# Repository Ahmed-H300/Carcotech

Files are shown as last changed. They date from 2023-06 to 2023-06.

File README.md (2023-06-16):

# Table of content
  * [preface](#preface)
  * [car design](#car-design)
  * [components, prices and links](#components-prices-and-links)
  * [schematics](#schematics)
  * [demo videos](#demo-videos)
  * [android app](#android-app)
  * [Important Notes](#Important-Notes)

# preface

<details>
<summary> click to view...</summary>

our problem statment was to create a car that follows a line without drifting out of the line and traverse a maze to find a specific path from end to end, the car have a small user interface via buttons, can play song and produce various patterns on strip of neopixel leds while traversing the maze or running on the line tracker, all without affecting the main functionality of the car, this wouldn't have been possible without the help of freeRTOS and espressif-idf.

### An autonomous car that can follow a line, solve maze and find it's path out. 
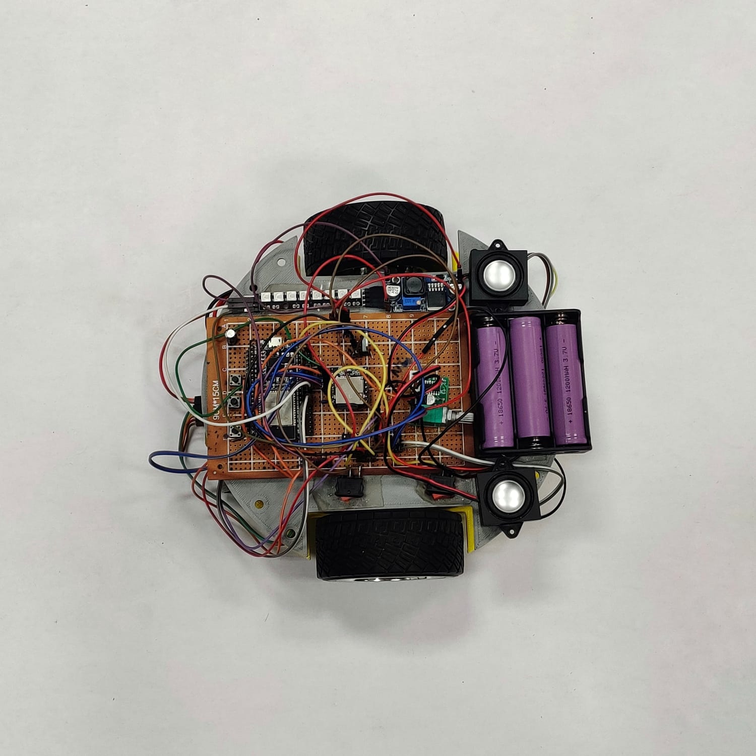
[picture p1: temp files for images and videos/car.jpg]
our lovely car


### shape of line tracker that was given to us to train on 
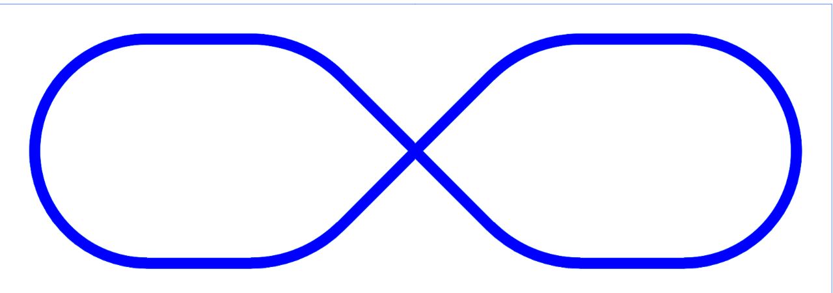
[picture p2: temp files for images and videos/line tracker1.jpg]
line tracker1


### shape of line tracker that was given on compitition day 
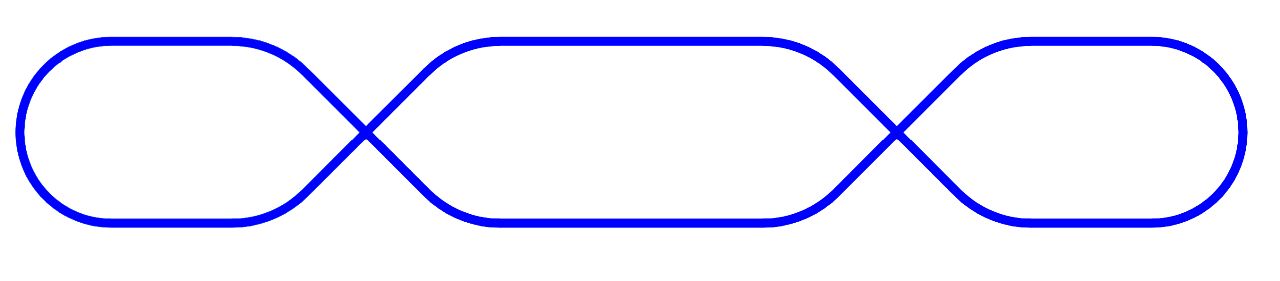
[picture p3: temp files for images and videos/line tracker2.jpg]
line tracker2


### shape of maze that was given to us and used on competition day
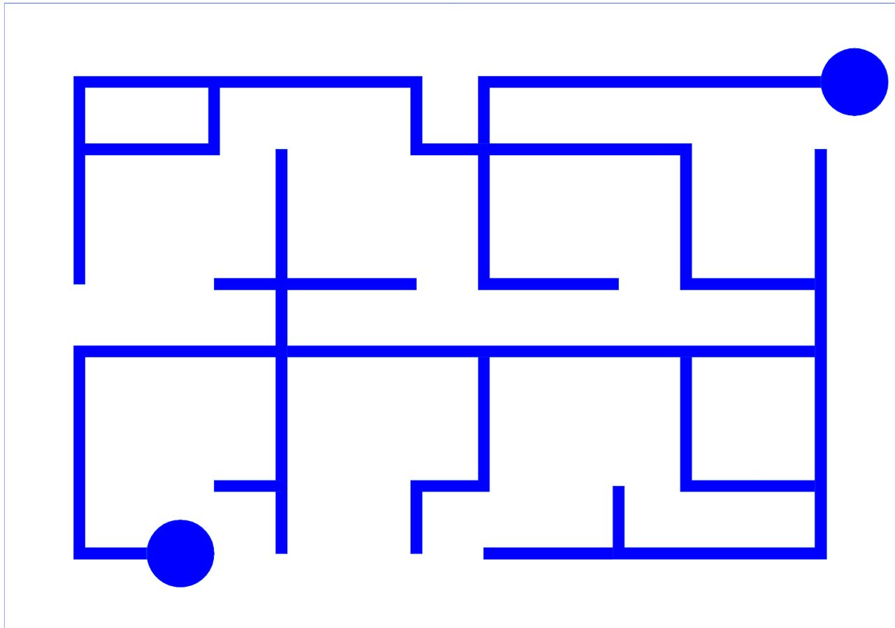
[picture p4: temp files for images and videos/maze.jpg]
maze


</details>

# car design

<details>
<summary> click to view...</summary>

- we used [freeCAD](https://www.freecad.org/) to design our car body, the design files can be found in [3D car design files/freeCAD-project files](./3D%20car%20design%20files/freeCAD-project%20files/) and you can open it using freeCAD, at first we designed the car to be of 3 floors and designed a holder for the sensor but after printing a prototype of the design, it was found that files called `third floor.FCStd` and `first_floor.FCStd` are only the useful file and all of the rest of design files were not used for the sake of this project.

- to print the 3d design, you need to generate STL files from your design (was done by freeCAD also), so the generated stl files are found in [3D car design files/stl files for 3 printing](./3D%20car%20design%20files/stl%20files%20for%203%20printing/) where `1st - floor.stl` and `3rd - floor.stl` are only files that we printed where each files is printed alone and you shall send the `.stl` files to the 3D printing service company not the `.FCStd` files.

- we made a custom design not a readily printed one as we needed a custmized shape, surface area and customized space for PCB and 2 motors, we choosed a circular shape as it seems to be a nice modern shape and it was inspired by [Pololu car](https://www.youtube.com/watch?v=mJV-KDqHgDQ)

## image of the final designed
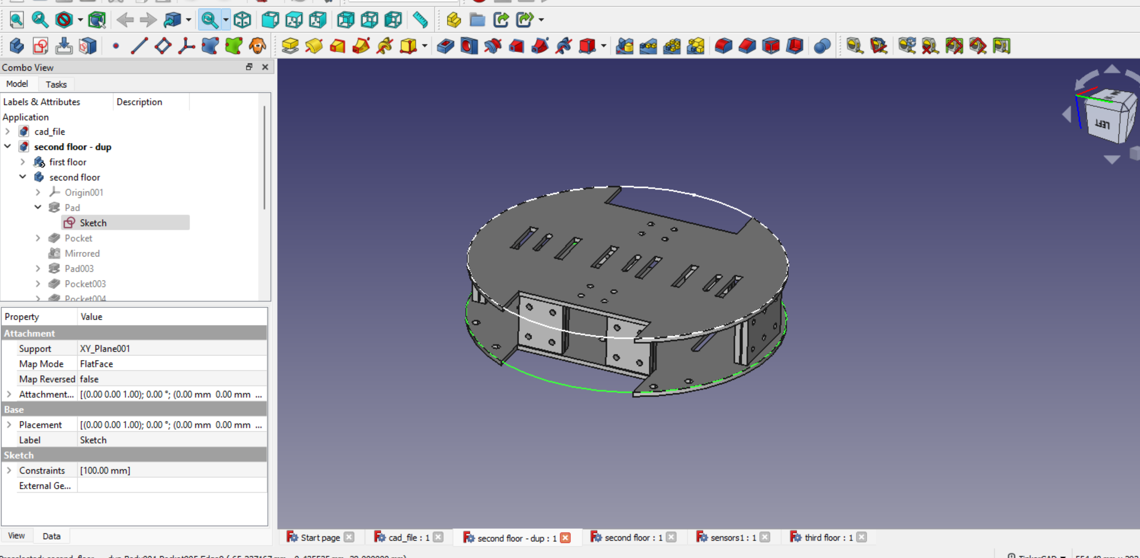
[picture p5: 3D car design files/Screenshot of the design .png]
final car body


</details>

# components, prices and links

<details>
<summary> click to view...</summary>

you can find the list of components with prices in the directory called [prices & components used](./prices%20%26%20components%20used/) in the `prices and components list.pdf` or `prices and components list.xlsx` but it's not mentioned where we purchased these components and the prices doesn't include custom costs nor the shipping prices.

**if you have time, we recommend you to purchase all of the components from ali express as it's cheaper in prices** 

| component | no.of items | unit price | link | extra details|
| :--- | :----: |  :----: | :--- | :--- |
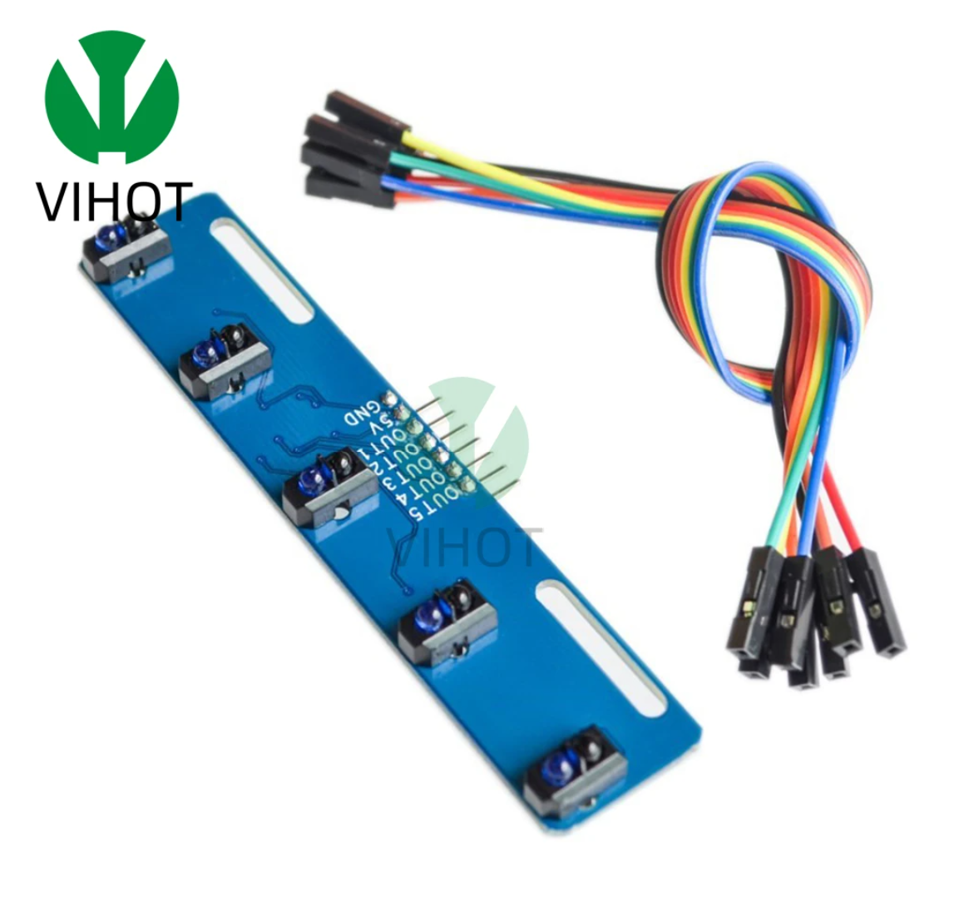
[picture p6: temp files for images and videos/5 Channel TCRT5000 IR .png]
5 Channel TCRT5000 IR
| 5 Channel TCRT5000 IR  | 2 | 50 EGP | https://www.aliexpress.com/item/1005004984933041.html?spm=a2g0o.order_list.order_list_main.25.21ef1802DzQBHj | used to detect line, intersections, path, etc...| 5 Channel TCRT5000 IR |
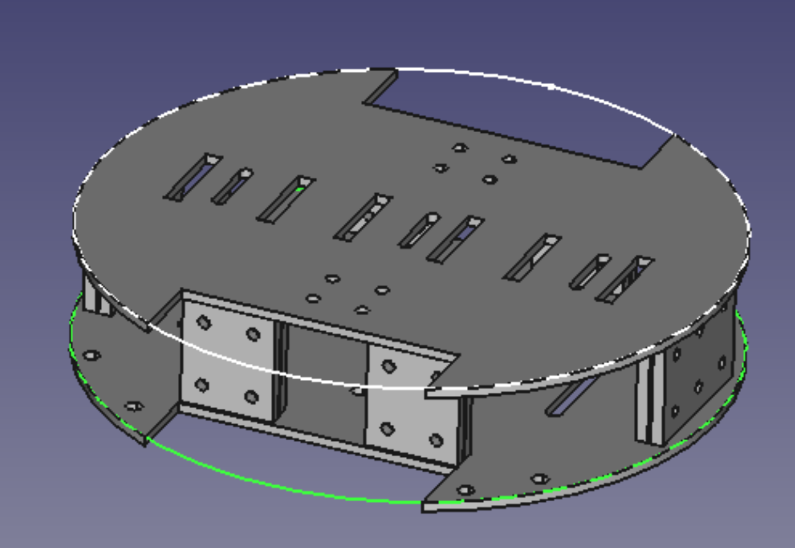
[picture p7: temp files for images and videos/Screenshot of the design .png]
3D printing (Car Chassis)
| 3D printing (Car Chassis)  | 1 | 460 EGP | https://wa.me/+201228206436 and https://wa.me/+201203414479 | this is the car body, there are plenty of companies, individuals whom provide 3d printing services, but these 2 numbers are for students who provide 3d printing services for a good quality with cheap prices | 3D printing (Car Chassis)
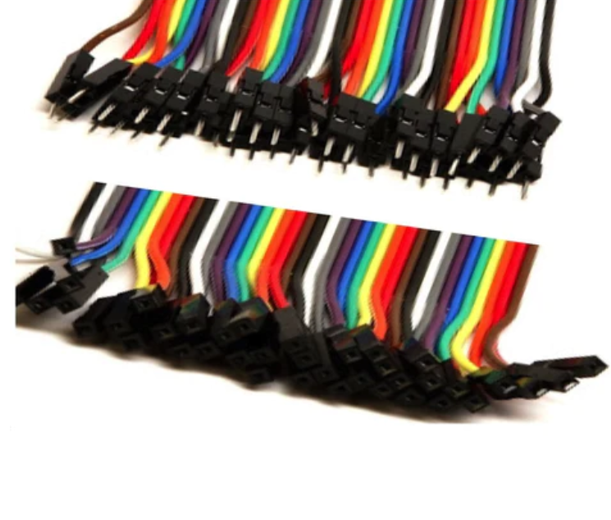
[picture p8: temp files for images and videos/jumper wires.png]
wires
| wires  | 40 | 1 EGP | https://store.fut-electronics.com/search?type=product&q=jumper+wire | was used to connect compoents with each other, future electronics provides jumper wires with many different lengths ( we used 30 cm and 20 cm wire) | wires
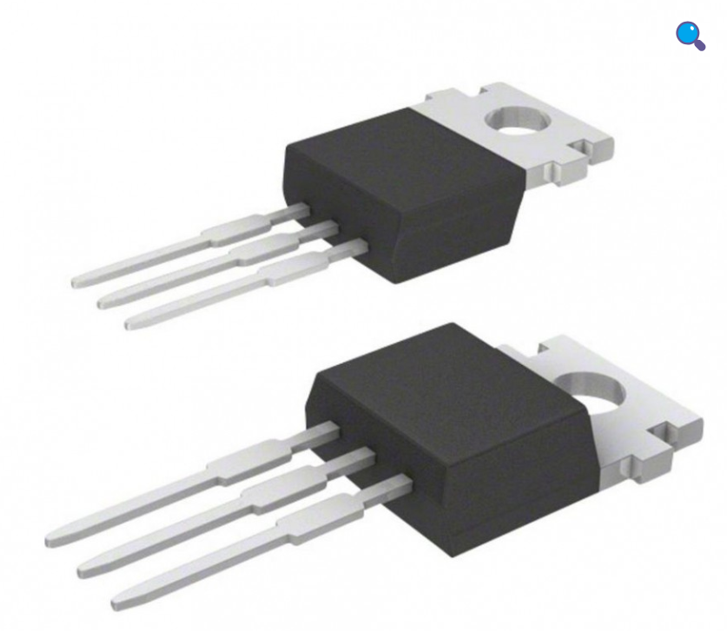
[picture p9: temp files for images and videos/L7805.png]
voltage regulator (L7805)
| voltage regulator (L7805)  | 1 | 4.5 EGP | https://free-electronic.com/product/l7805cv/ | supplied esp32 with the power supply of 5V, we had to insulate the power source of esp32 from other components as speakers made small fluctuations in the power source which made esp32 to reset several times | voltage regulator (L7805)|
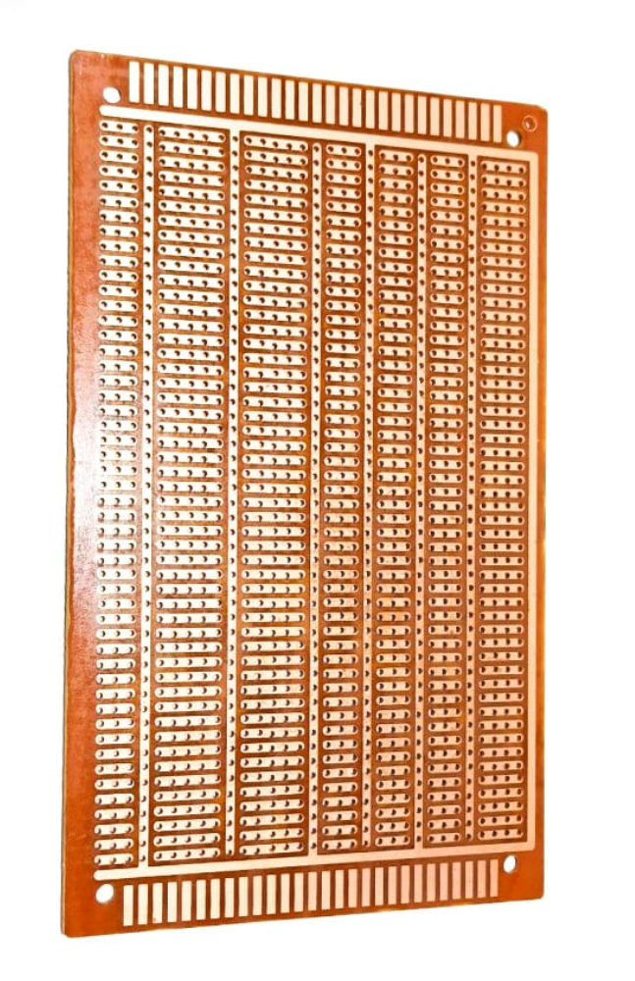
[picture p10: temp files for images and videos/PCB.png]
PCB Bread Board Shape FR2 (9X15 cm2)
| PCB Bread Board Shape FR2 (9X15 cm2)  | 2 | 15 EGP | https://free-electronic.com/product/pcb-bread-board-shape-fr2-9x15-cm2-horizontal/ | we used a prototype pcb which is more reliable than solderless board | PCB Bread Board Shape FR2 (9X15 cm2) |
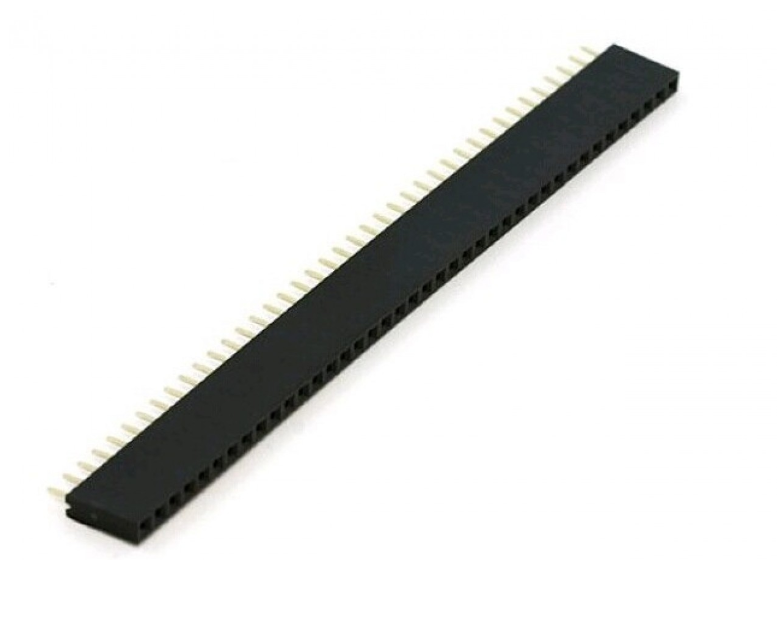
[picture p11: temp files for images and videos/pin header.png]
pin header
| pin header  | 8 | 4 EGP | https://free-electronic.com/?s=pin+header&product_cat=0&post_type=product | needed pin headers to be soldered onto prototype pcb (we mainly used female pin header and rarely male pin headers) | pin header |
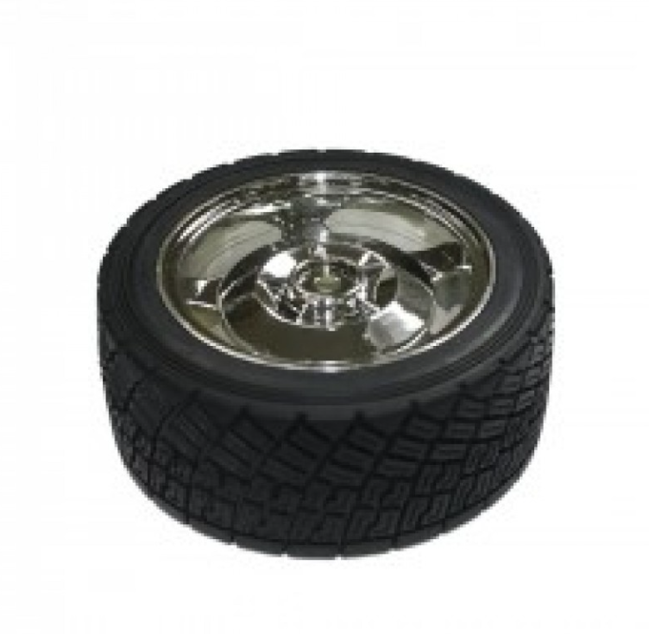
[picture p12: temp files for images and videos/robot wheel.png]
Robot Car Wheel 85mm
| Robot Car Wheel 85mm  | 2 | 85 EGP |  https://free-electronic.com/product/robot-car-wheel-85mm/ | this was the perfect wheel for our car body the provided needed height from the ground | Robot Car Wheel 85mm | 
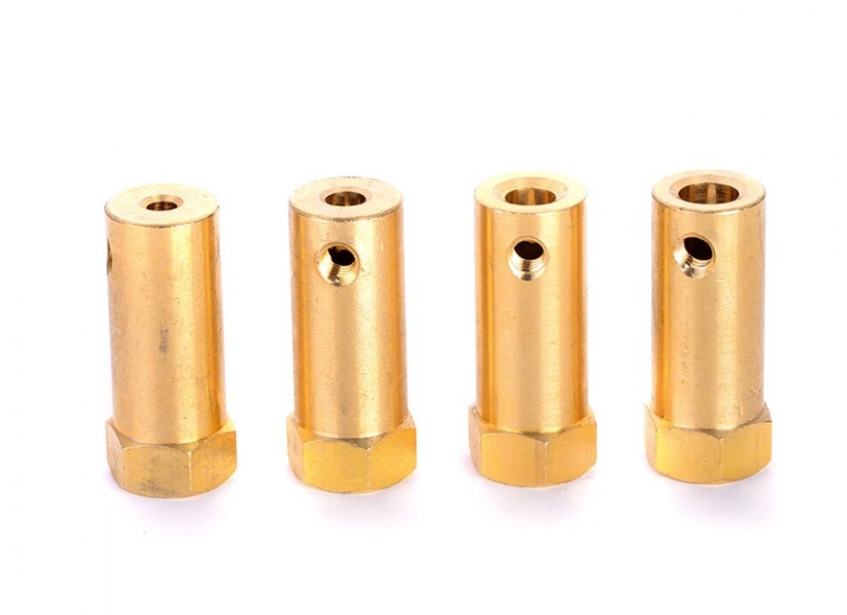
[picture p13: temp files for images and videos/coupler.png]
Metal Coupler 4mm
| Metal Coupler 4mm  | 2 | 35 EGP | https://free-electronic.com/product/metal-coupler-4mm-short-coupling-for-robot-smart-car-wheel/ |  was used to connect the motors to the wheels | Metal Coupler 4mm |
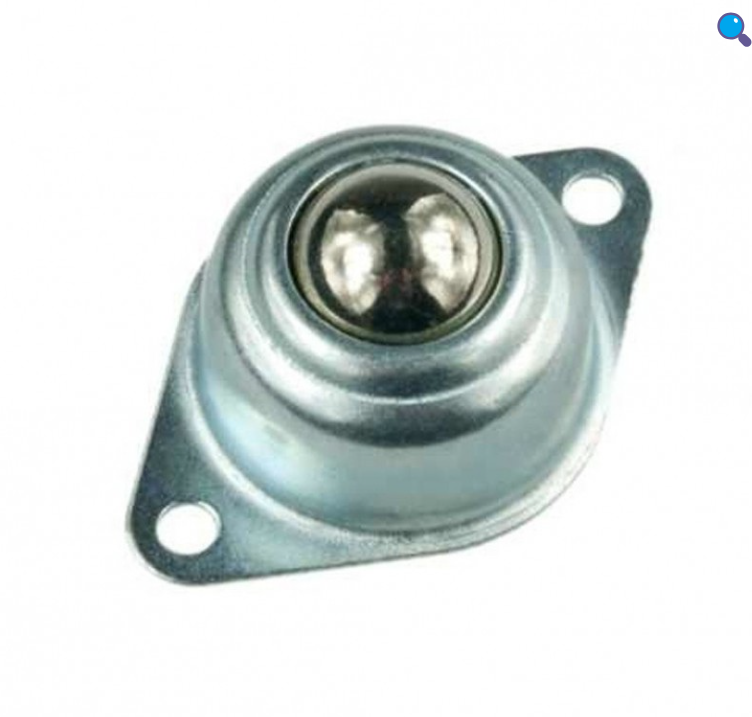
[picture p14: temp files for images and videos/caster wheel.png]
Metal Caster Wheel for Robot (20mm)
| Metal Caster Wheel for Robot (20mm)  | 2 | 35 EGP | https://free-electronic.com/product/metal-caster-wheel-for-robot-20mm/ | since car has only 2 motors so we needed 2 caster wheel to support car body from beneath to prevent it from swinging | Metal Caster Wheel for Robot (20mm) |
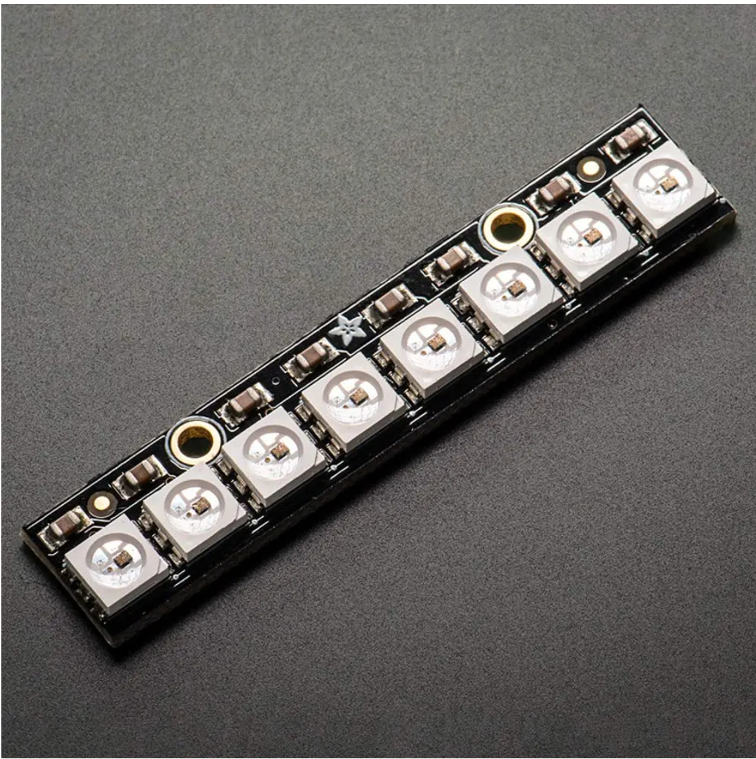
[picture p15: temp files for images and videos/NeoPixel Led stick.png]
NeoPixel Led stick
| NeoPixel Led stick  | 1 | 200 EGP | https://www.aliexpress.com/i/4000203985307.html | I bought this component before a year from ram-electronics but it seems now it's not available on ram any more but it's available on ali express | NeoPixel Led stick
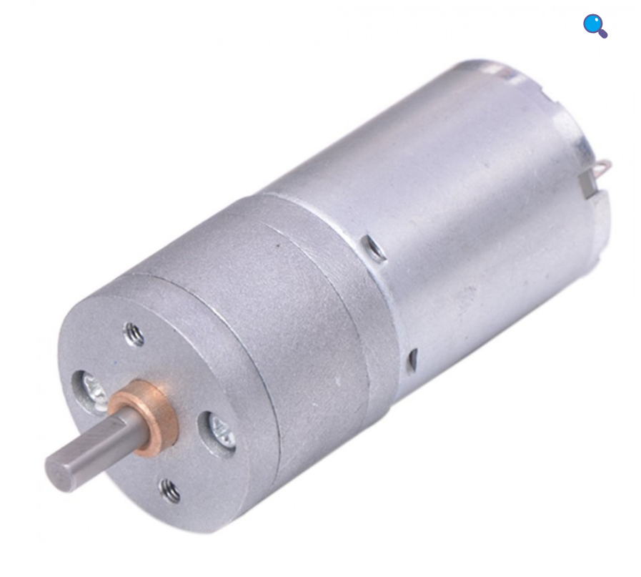
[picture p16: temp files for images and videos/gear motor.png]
DC Gear Motor (8.8KG ) 250RPM
| DC Gear Motor (8.8KG ) 250RPM   | 2 | 325 EGP | https://free-electronic.com/product/dc-gear-motor-8-8kg/ | criteria of selection of our gear motor is that it has high reduction ration with high torque and high rpm but note that rpm is inversely proportional to reduction ratio so our motor had torque of 8.8 KG with rpm = 250 RPM and reduction ration 25:1 but it worked perfectly | DC Gear Motor (8.8KG ) 250RPM
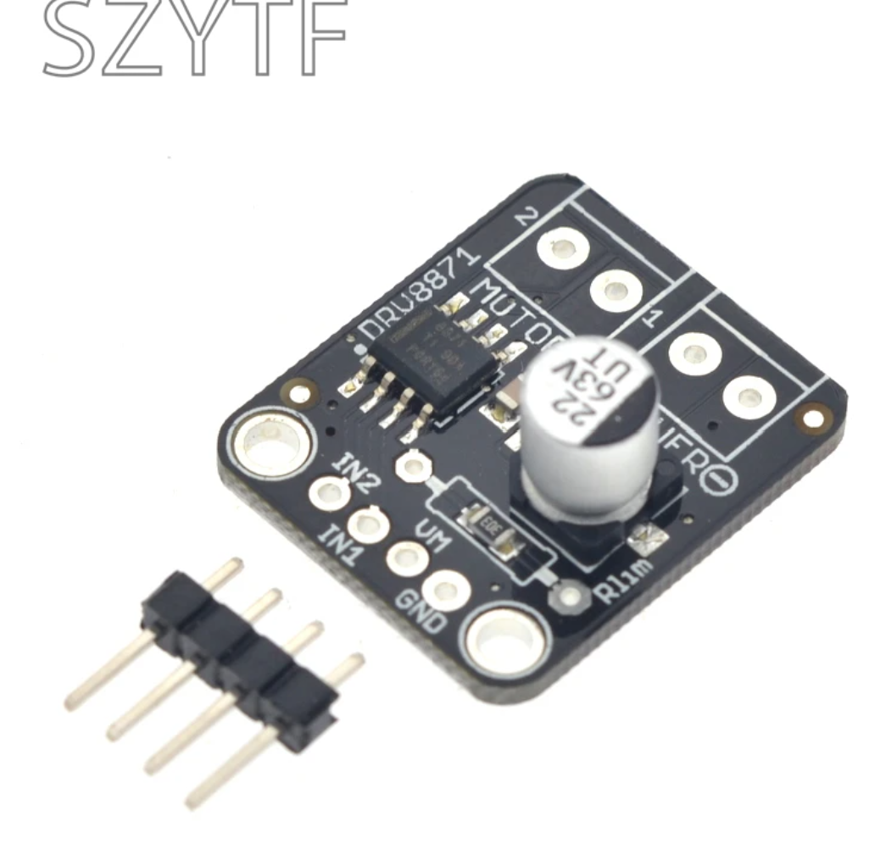
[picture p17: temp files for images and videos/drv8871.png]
Motor driver DRV8871
| Motor driver DRV8871  | 2 | 130 EGP | https://www.aliexpress.com/item/1005001590487986.html?spm=a2g0o.order_list.order_list_main.40.21ef1802DzQBHj | motor driver small chip where one chip controls one motor so we needed 2, this is better than L298 as it's smaller, can pass higher current | Motor driver DRV8871 |
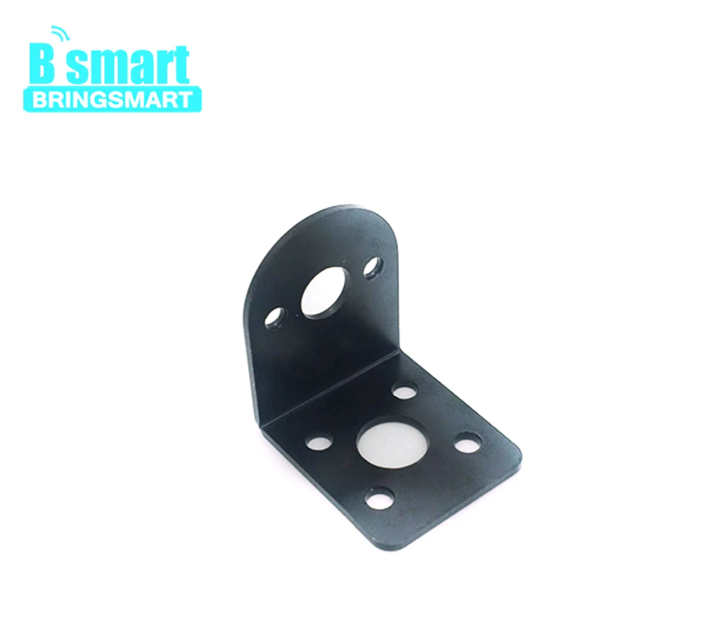
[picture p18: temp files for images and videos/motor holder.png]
Screw Mounting Bracket
|  Screw Mounting Bracket  | 2 | 50 EGP | https://www.aliexpress.com/item/32856826638.html?spm=a2g0o.order_list.order_list_main.89.21ef1802DzQBHj | used to hold the motor onto the car body | Screw Mounting Bracket |
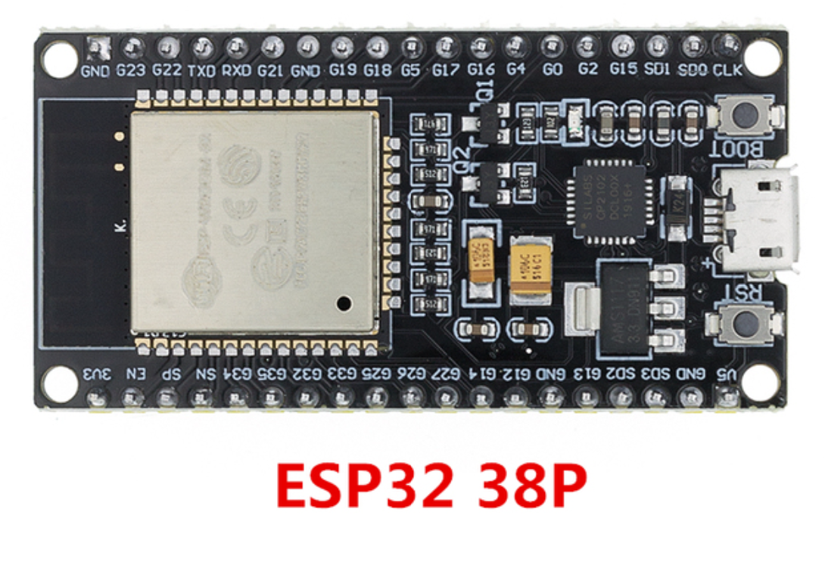
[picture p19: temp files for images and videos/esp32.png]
ESP32 Development Board
| ESP32 Development Board  | 1 | 150 EGP | https://www.aliexpress.com/item/1005001621773806.html?spm=a2g0o.order_list.order_list_main.95.21ef1802DzQBHj | this was our main MCU and we recommend using it over arduino as it has many useful features like its espressif-idf that comes with freeRTOS, dual core, high speed MCU (240 MHZ), integrated wifi and integrated bluetooth on chip| ESP32 Development Board |
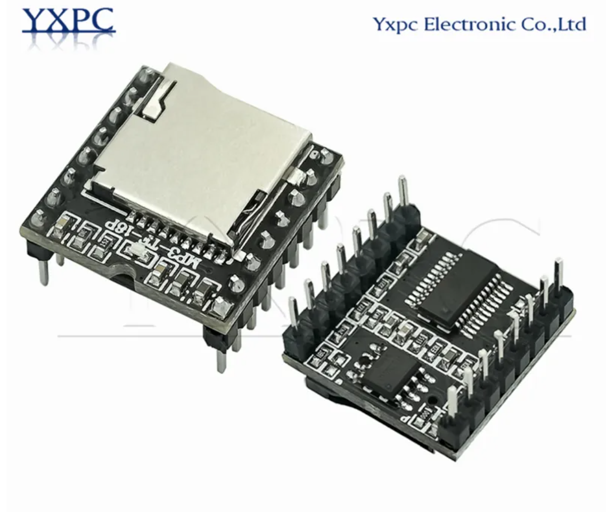
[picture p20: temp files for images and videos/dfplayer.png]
DFPlayer Mini MP3
| DFPlayer Mini MP3  | 1 | 50 EGP | https://www.aliexpress.com/item/1005004994130177.html?spm=a2g0o.order_list.order_list_main.70.21ef1802DzQBHj | a chip that plays mp3 audios without need of continous interaction with MCU, you just give it mp3 file number using MCU and it will play it for you | DFPlayer Mini MP3 |
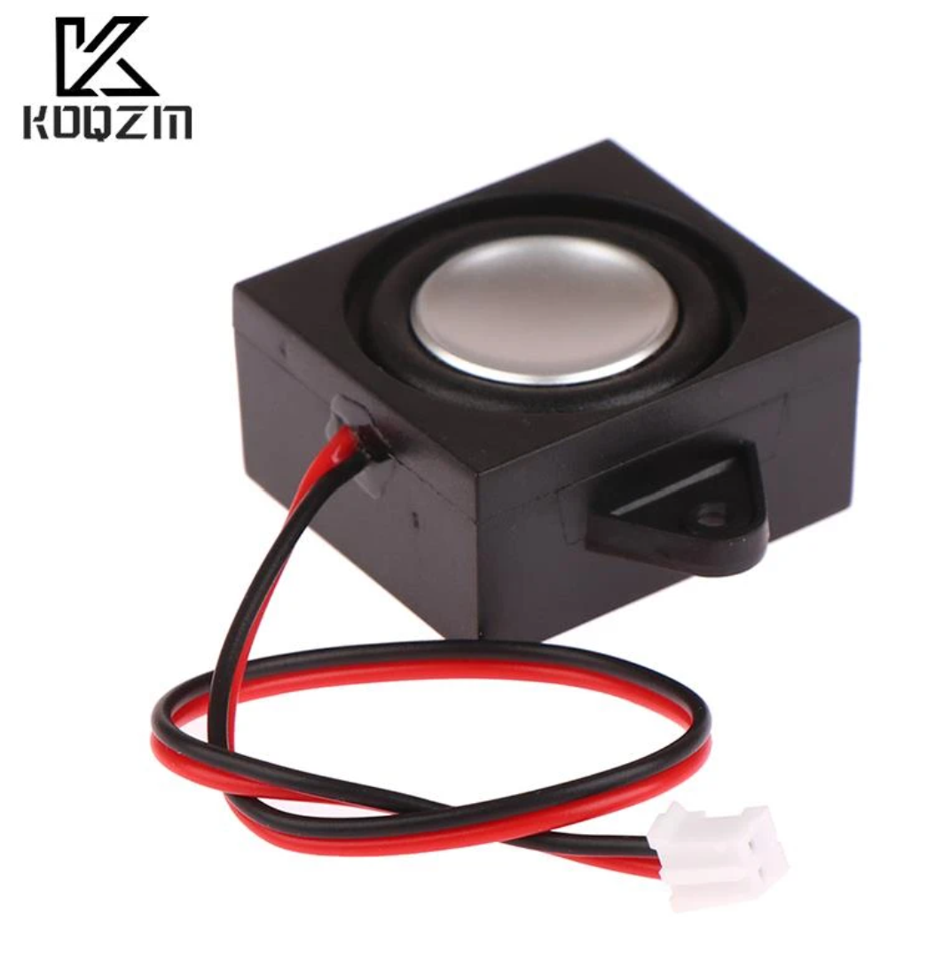
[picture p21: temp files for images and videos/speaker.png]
Speaker 4 Ohm 3 Watt
| Speaker 4 Ohm 3 Watt  | 2 | 55 EGP | https://www.aliexpress.com/item/1005005020984275.html?spm=a2g0o.order_list.order_list_main.15.21ef1802DzQBHj | speakers used to output sound and music while traversing | Speaker 4 Ohm 3 Watt |
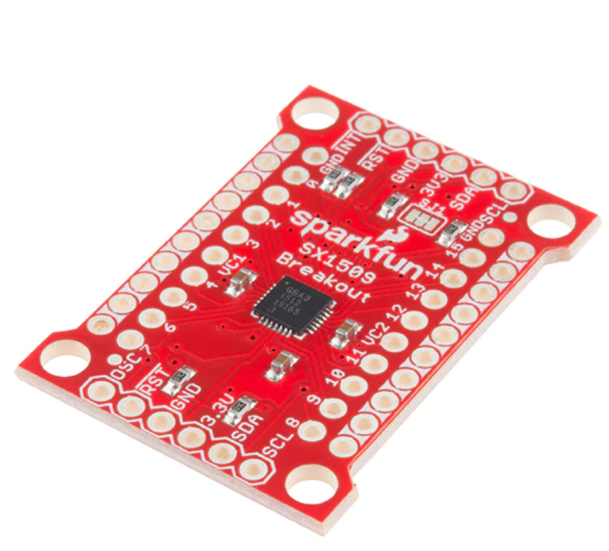
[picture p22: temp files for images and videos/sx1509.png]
I/O Expander Breakout - SX1509
| I/O Expander Breakout - SX1509  | 1 | 85 EGP | https://store.fut-electronics.com/products/copy-of-bi-directional-voltage-level-translator-shifter-txb0104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 | since the amount of pins on esp32 wouldn't be enough for all components, we used a port expander that communicates with esp32 through I2C that will increase the number of pins available | I/O Expander Breakout - SX1509 |
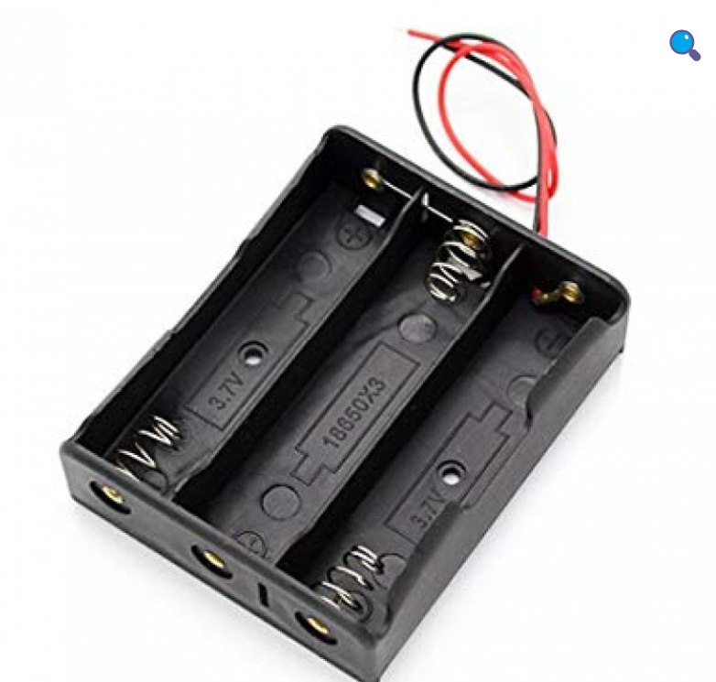
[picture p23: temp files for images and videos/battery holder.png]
battery holder ( 3 x 18650 )
| battery holder ( 3 x 18650 )  | 1 | 15 EGP | https://free-electronic.com/product/battery-holder-3-x-18650/ | holder for lithium batteries as our car runs on 3 lithium batteries | battery holder ( 3 x 18650 ) |
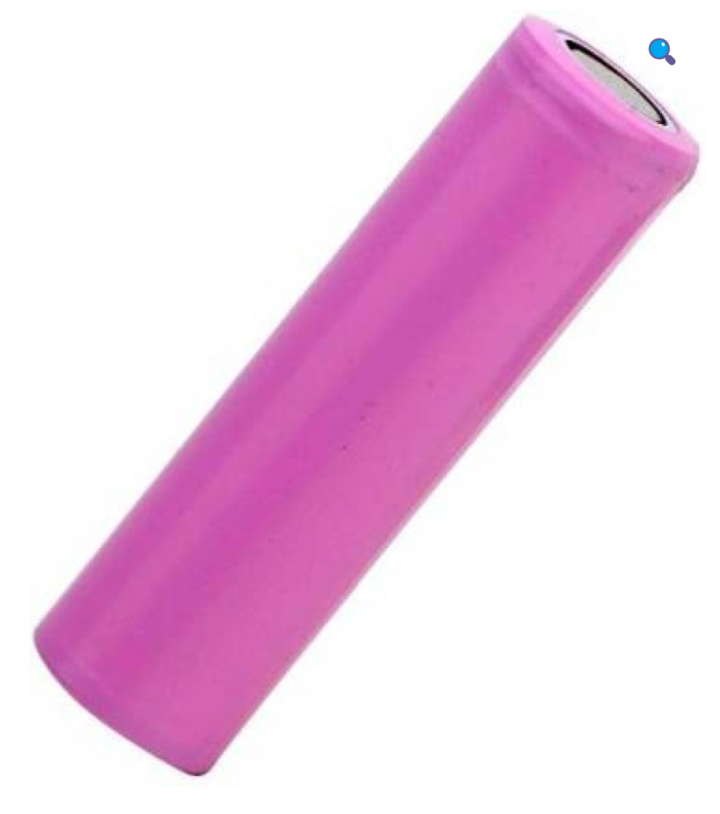
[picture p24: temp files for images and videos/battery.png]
Rechargeable Li-ion Battery18650
| Rechargeable Li-ion Battery18650  | 3 | 50 EGP | https://free-electronic.com/product/rechargeable-li-ion-battery18650-3-7v-1200mah/ | used as power source for the car | Rechargeable Li-ion Battery18650 | 
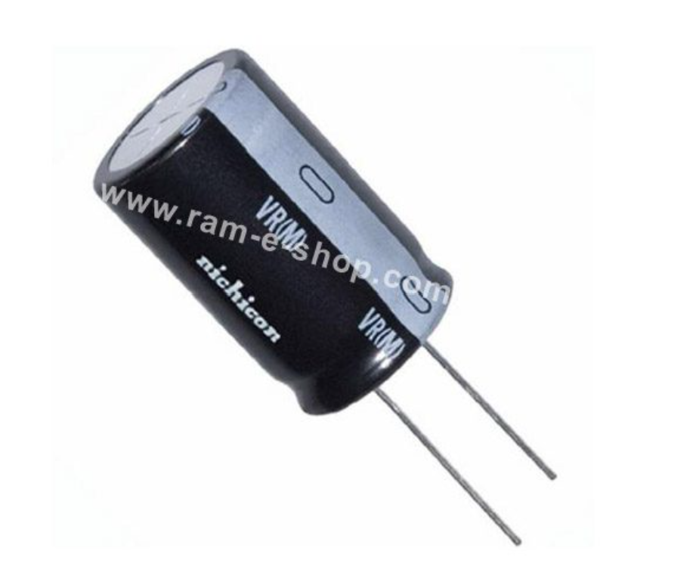
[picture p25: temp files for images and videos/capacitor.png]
electrolytic capacitor
| electrolytic capacitor (25V - 60 micro farad)  | 1 | 3 EGP | https://ram-e-shop.com/product/c-47u250v/ | was used to be connected between 3.3v and GND that helps in power source stability | electrolytic capacitor |
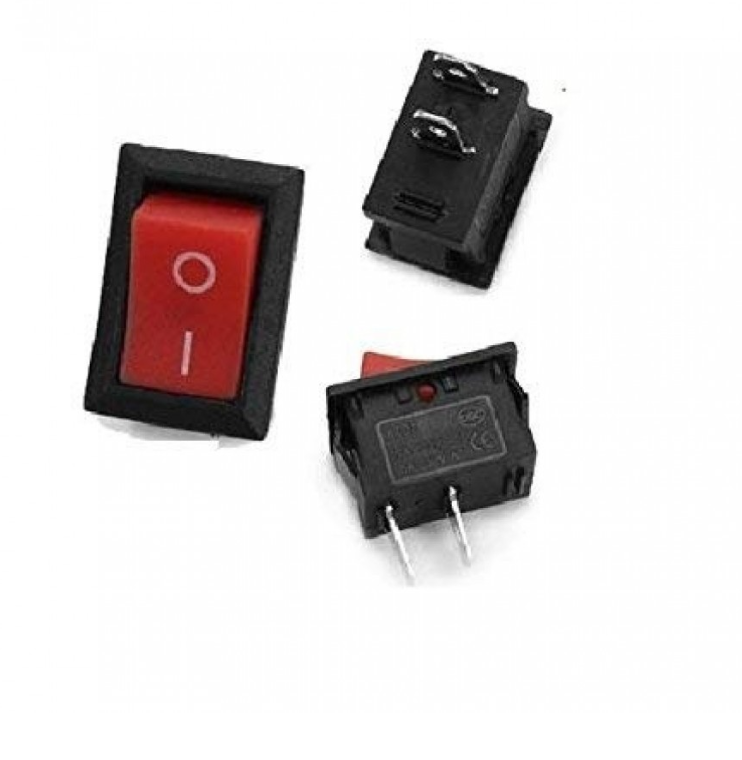
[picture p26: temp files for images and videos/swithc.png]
switch
| switches   | 2 | 1.5 EGP | https://free-electronic.com/product/boat-rocker-switch-on-off-6a250vac-kcd1/ | one used to switch on/off the battery from the system and second one to switch on/off esp32 from the system | switch |
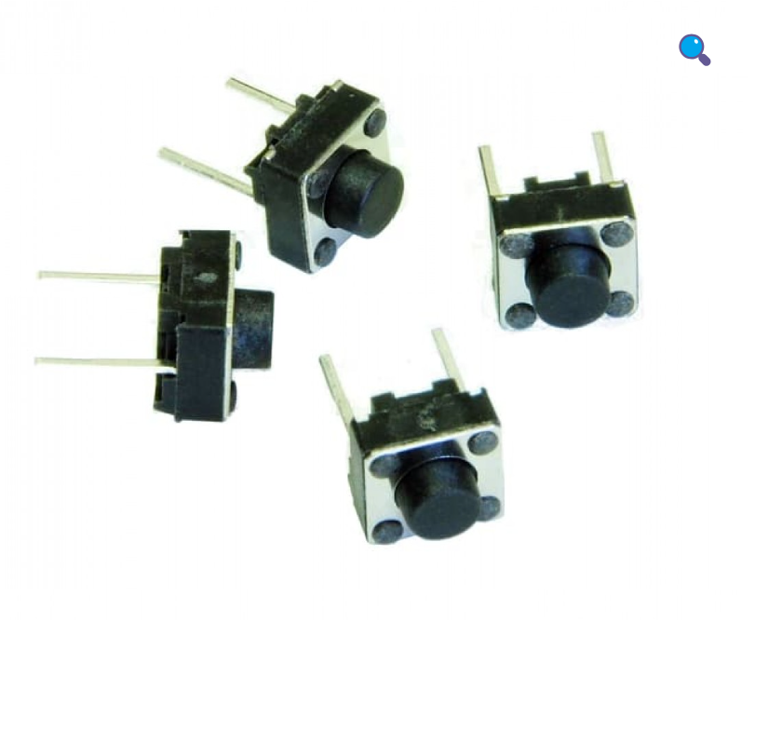
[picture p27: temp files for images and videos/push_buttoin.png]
push button
| push buttons  | 3 | 0.75 EGP | https://free-electronic.com/product/press-2pin-6x6/ | used as user interface , 1 for Line tracker (L) , 1 for maze trainer (M_t) , 1 for maze solver (M_s) | push button |
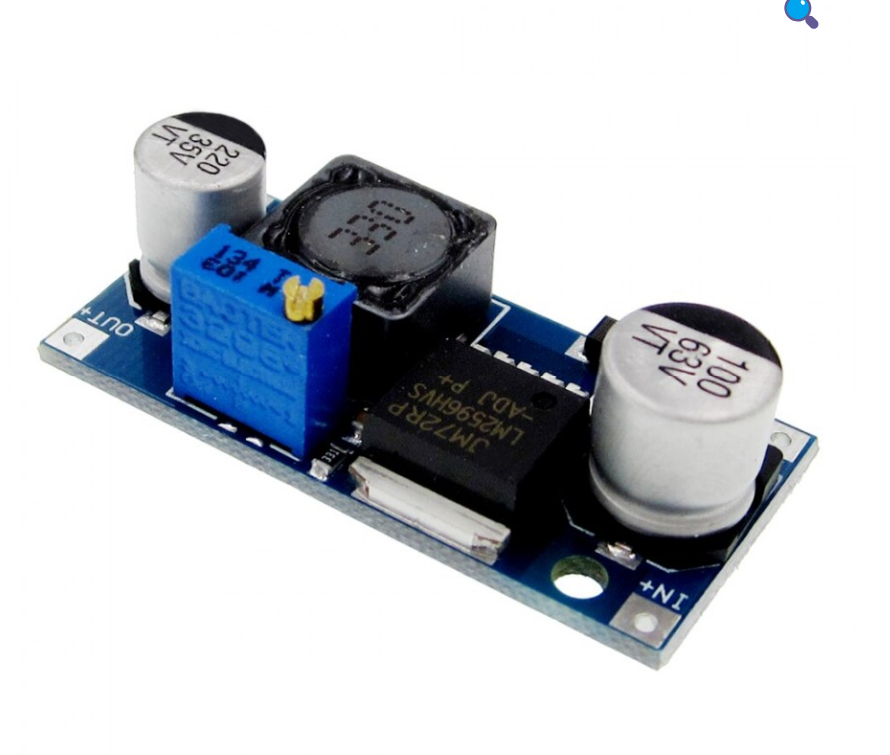
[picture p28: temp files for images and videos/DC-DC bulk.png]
DC-DC Step-Down Module
| LM2596HVS-ADJ DC-DC Step-Down Module (3A)  | 1 | 60 EGP | https://free-electronic.com/product/lm2596hvs-adj-dc-dc-step-down-module-3a/ | used to convert power supply from batteries (around 11 volt) to 3.3V to supply all the system of the car except esp32 that's supplied by voltage regulator and we didn't use voltage regulator to supply the whole system as the whole system withdraw a high amount of current and the maximum that a voltage regulator can supply is about 1 A| DC-DC Step-Down Module|
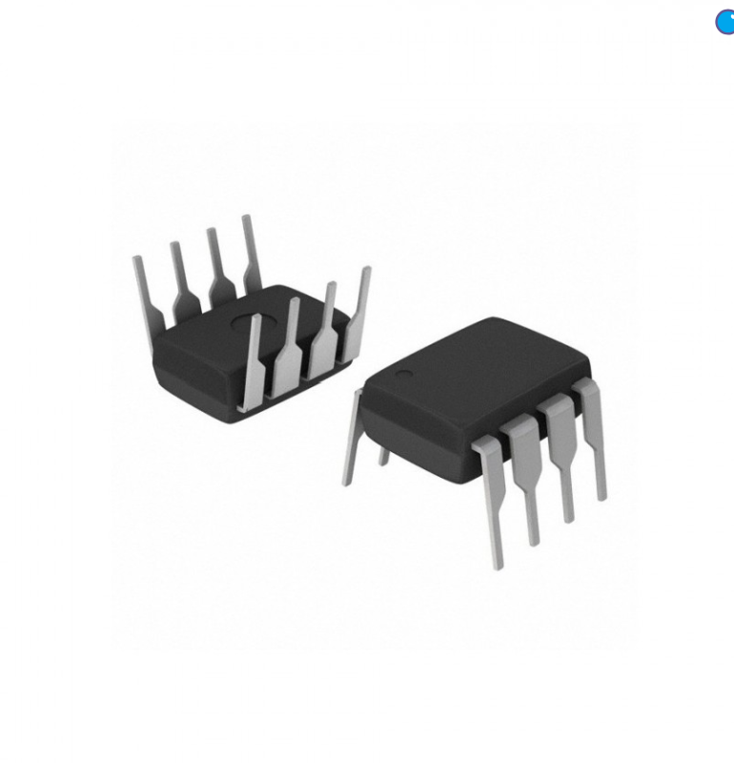
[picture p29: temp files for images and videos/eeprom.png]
EEPROM
| external EEPROM - 32 Kilo-byte (24C256)  | 1 | 25 EGP | https://free-electronic.com/product/24c256/ | was used to store the optimized path after traversing the maze as Esp32 doesn't have interal EEPROM so we bought external one to store the optimized path on it so that if the system shutdown (car was turned off), we don't have to train again as the path is already stored | EEPROM |
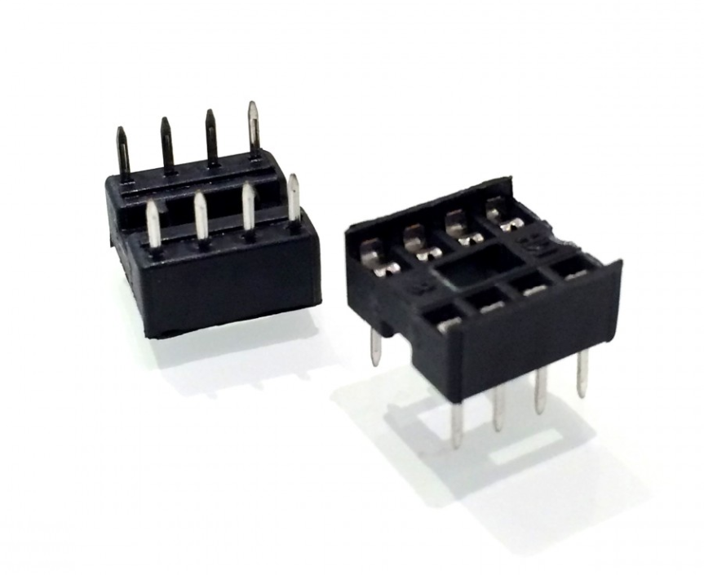
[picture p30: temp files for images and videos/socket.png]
IC socket
| IC SOCKET Base 8 PIN DIP for eeprom  | 1 | 0.5 EGP | https://free-electronic.com/product/ic-socket-base-8-pin-dip/ | we didn't solder EEPROM IC onto the pcb board directly but instead, we solder the IC socket and the eeprom is inserted to the socket so any time, you can change the eeprom | IC socket |
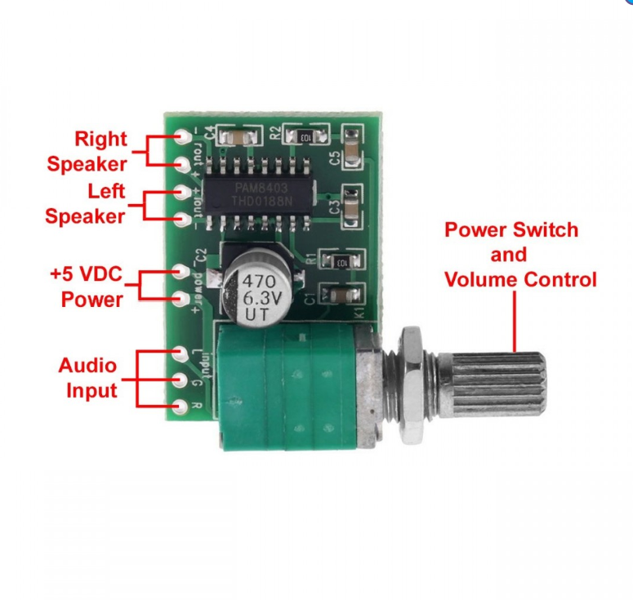
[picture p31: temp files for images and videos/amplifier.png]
amplifier
| PAM8403 5V Power Audio Amplifier Board  | 1 | 35 EGP | https://free-electronic.com/product/pam8403-5v-power-audio-amplifier-board/ | since the DFPlayer can output weak analog signal, the this amplifier module is used to amplify the signal before bypassing it to the speakers and the knob on it is used to control the volume | amplifier | 

</details>

# schematics

<details>
<summary> click to view...</summary>

- we made the schematics using [KICAD](https://www.kicad.org/) (one of the most free useful tools in PCB designs and schematics) where the KICAD project files can be found in the directory called [schematics files/KICAD project files](./schematics%20files/KICAD%20project%20files/) and the schematic itself is exported as pdf where it can be found in [schematics files/shematics view.pdf](./schematics%20files/shematics%20view.pdf)

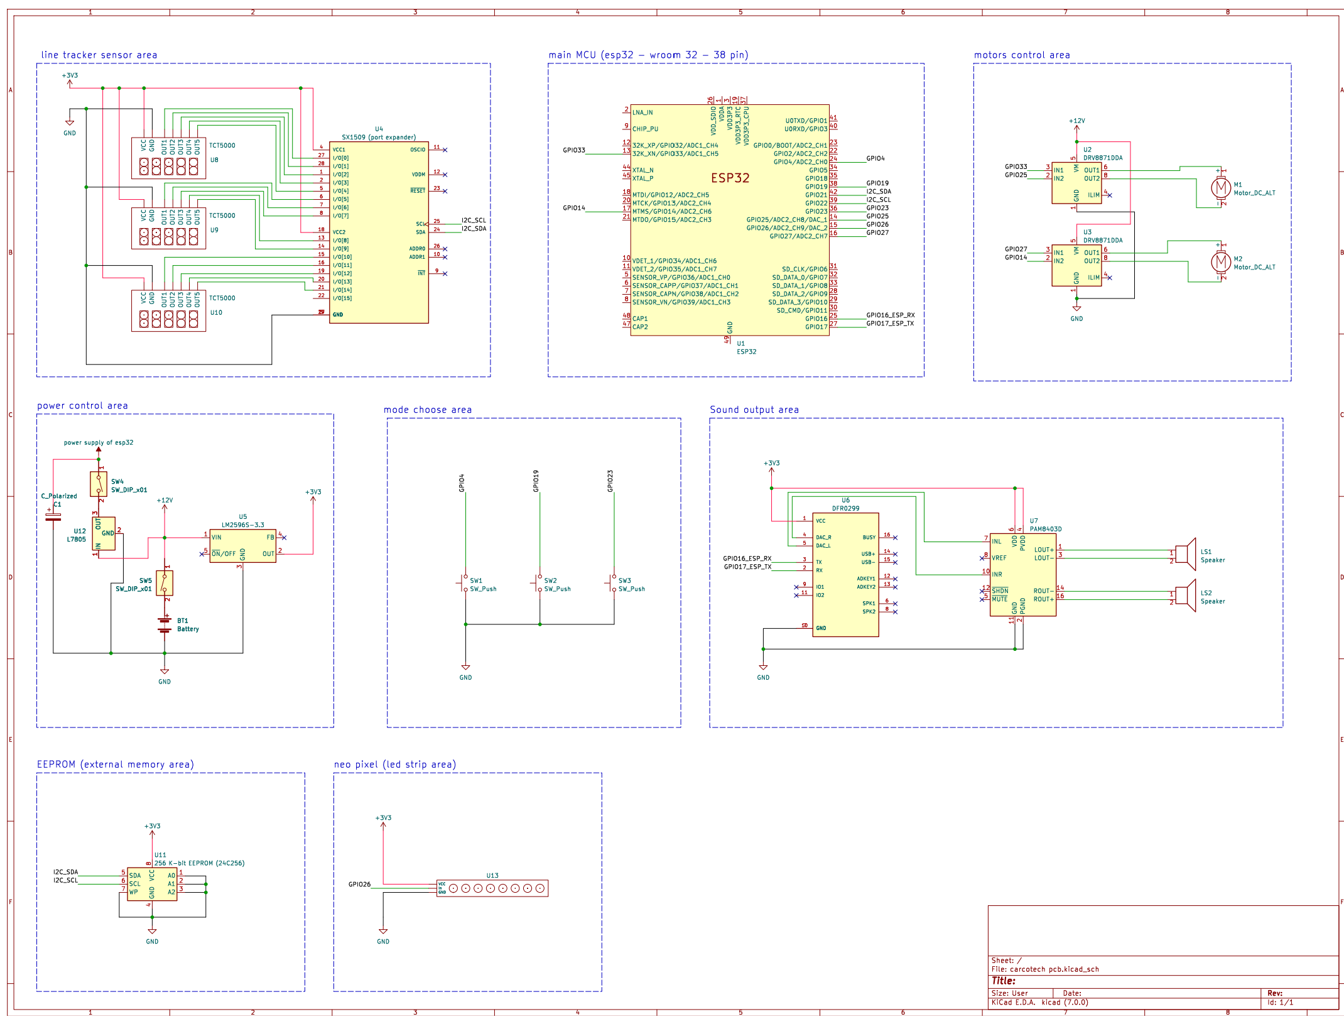
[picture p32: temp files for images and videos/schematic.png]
schematics


</details>

# demo videos

<details>
<summary> click to view...</summary>

## Line tracker 
### (click on image to view the video)
IMAGE ALT TEXT (http://www.youtube.com/watch?v=FVEoGQgsD1o "Line tracker on competition day")

## Maze trainer 
### (click on image to view the video)
IMAGE ALT TEXT (http://www.youtube.com/watch?v=uL8tybA_7e4 "Maze trainer on competition day")

## Maze solver 
### (click on image to view the video)
IMAGE ALT TEXT (http://www.youtube.com/watch?v=FgmfNq2BWTQ "Maze solver on competition day")

## Miscellaneous Videos
### (click on image to view the video)
---

### competition day line tracker with sound
IMAGE ALT TEXT (http://www.youtube.com/watch?v=pODliE_6rCc "Line tracker on competition day")

### random expriment 1 on Line tracker
IMAGE ALT TEXT (http://www.youtube.com/watch?v=ryqJlh_6-NY "Line tracker 1")

### random expriment 2 on Line tracker
IMAGE ALT TEXT (http://www.youtube.com/watch?v=IrJWMPCKxJE "Line tracker 2")

### competition day maze trainer with sound
IMAGE ALT TEXT (http://www.youtube.com/watch?v=vTmSzqmyeRo "maze trainer on competition day")

### random expriment 1 maze trainer 
IMAGE ALT TEXT (http://www.youtube.com/watch?v=PMsLQ8f5rEo "random maze trainer")

### random expriment 2 maze trainer 
IMAGE ALT TEXT (http://www.youtube.com/watch?v=YR6AI_VsmS8 "random maze trainer")

### random expriment 3 maze trainer 
IMAGE ALT TEXT (http://www.youtube.com/watch?v=V4b4zh7_W2g "random maze trainer")

### random expriment 4 maze trainer 
IMAGE ALT TEXT (http://www.youtube.com/watch?v=Yapoz3KJym8 "random maze trainer")

### competition day maze solver with sound
IMAGE ALT TEXT (http://www.youtube.com/watch?v=Ea6kgzUnRns "maze solver on competition day")

### random expriment maze solver 
IMAGE ALT TEXT (http://www.youtube.com/watch?v=8YGnpCDjReU "random maze solver")

### random expriment 1 maze solver & maze trainer
IMAGE ALT TEXT (http://www.youtube.com/watch?v=6LpIFKPfciE "random maze")

### random expriment 2 maze solver & maze trainer
IMAGE ALT TEXT (http://www.youtube.com/watch?v=ktwz5GvXBHs "random maze")

</details>

# android app

<details>
<summary> click to view...</summary>

- the app can be found on [google play sore](https://play.google.com/store/apps/details?id=com.carcotech.maze_solver) 

- whereas the code can be found in the directory called [android code](./android%20code/)

- we used android app only in the line tracker as the mobile application sends "H" via bluetooth to the car to tell it that it's running on a straight so move faster or send "L" via bluetooth to the car to tell it that it's not running on a straight so move slower 

<p align="center">
    Material Bread logo
</p>

</details>

# Important Notes

<details>
<summary> click to view...</summary>

1. we used freeRTOS that comes with espressif-idf.
2. code can be found in [ESP32 code/Carcotech/](./ESP32%20code/Carcotech/) where the project is made using [platformIO](https://platformio.org/) (platformIO is just vscode extension that can be downloaded), we recommend using platformIO over arduinoIDE as you can manage code more professionaly on vscode than on arduino IDE.
3. to open the project, open platformIO and click open project where the project working directory is `ESP32 code/Carcotech/`, also note that we used alot of libraries where some of them aren't included in the project files but they are present in platformIO repo, so once you open the project using platformIO, platformIO will download these libraries from its repo.
4. if you couldn't understand the code, [here](https://youtu.be/uo7UUR3-JVw) is a video for explanation of the code but note that the video is in arabic.
5. in the directory called [datasheet of some components](./datasheet%20of%20some%20components/), as the name implies, you can find some of the datasheets and reference manual of the components that we used .
6. name of libraries that are not included in this project files are found in the file called [platformIO.ini](./ESP32%20code/Carcotech/platformio.ini) where the libraries are 
    -   dfrobot/DFRobotDFPlayerMini @ 1.0.5
    -   https://github.com/RobTillaart/I2C_EEPROM
    -   https://github.com/adafruit/Adafruit_NeoPixel 

</details>

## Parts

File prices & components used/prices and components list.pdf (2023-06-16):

component | no.of.items unit price total
5 Channel TCRT5000 IR | 3 | 32.75 | 98.25
3D printing (Car Chassis) | 1 | 460 | 460
wires | 40 | 0.75 | 30
voltage regulator (L7805) | 1 | 5 | 5
PCB DOT FR2 (9X15 cm2) | 2 | 14 | 28
pin header | 8 | 3.5 | 28
Robot Car Wheel 85mm | 2 | 85 | 170
Metal Coupler 4mm | 2 | 35 | 70
Metal Caster Wheel for Robot (20mm) | 2 | 35 | 70
NeoPixel Led strip | 1 | 100 | 100
DC Gear Motor (8.8KG ) 250RPM | 2 | 325 | 650
Motor driver DRV8871 | 2 | 102 | 204
Screw Mounting Bracket | 2 | 25 | 50
ESP32 Development Board | 1 | 115 | 115
DFPlayer Mini MP3 | 1 | 25 | 25
Speaker 4 Ohm 3 Watt | 2 | 50 | 100
I/O Expander Breakout - SX1509 | 1 | 85 | 85
battery holder ( 3 x 18650 ) | 1 | 15 | 15
Rechargeable Li-ion Battery18650 | 3 | 45 | 135
capacitor (25V - 60 micro farad) | 1 | 0.5 | 0.5
switches | 3 | 0.75 | 2.25
LM2596HVS-ADJ DC-DC Step-Down Module (3A) | 1 | 60 | 60
turn on switch | 2 | 1.5 | 3
IC socked with EEPROM | 1 | 30 | 30
PAM8403 5V Power Audio Amplifier Board | 1 | 35 | 35
| | | 2569
Total amount of essential components | 2309
Total amount of unessential components | 260
Total Amount | 2569

Note: cells colored in yellow are not essential components while cells colored in green are essential components in the car

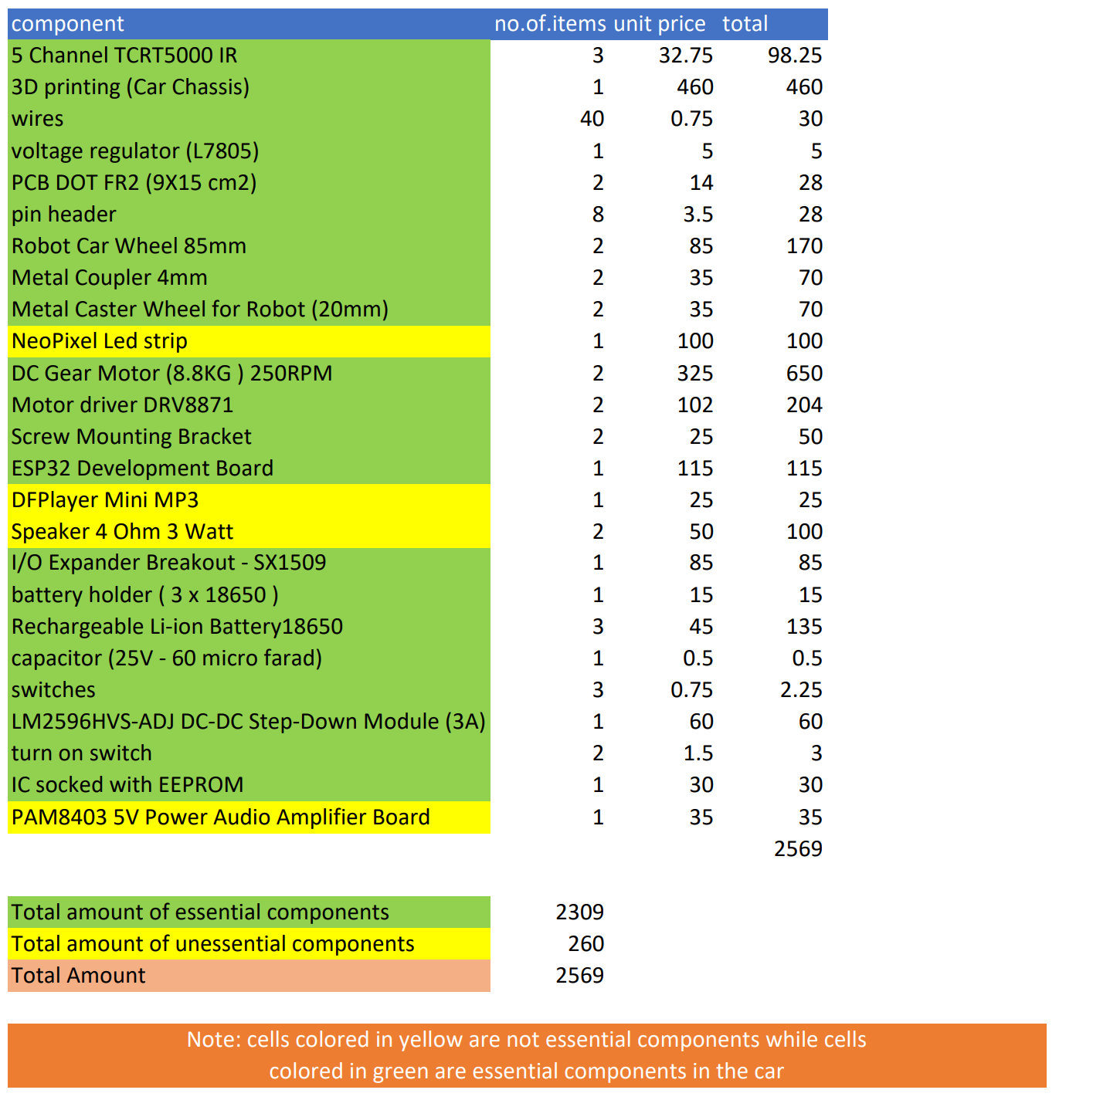
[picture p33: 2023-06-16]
temp files for images and videos/component_prices.png

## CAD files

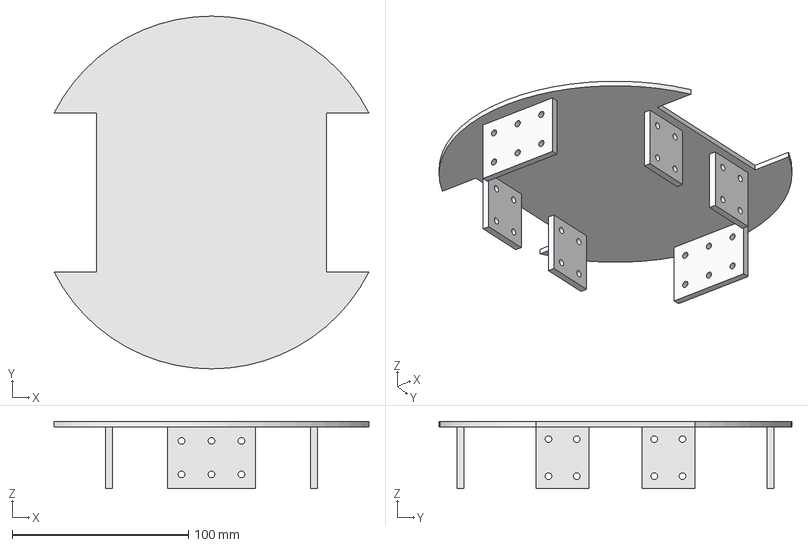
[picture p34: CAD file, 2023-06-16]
3D car design files/freeCAD-project files/third floor.FCStd
178.6 x 200.0 x 38.0 mm

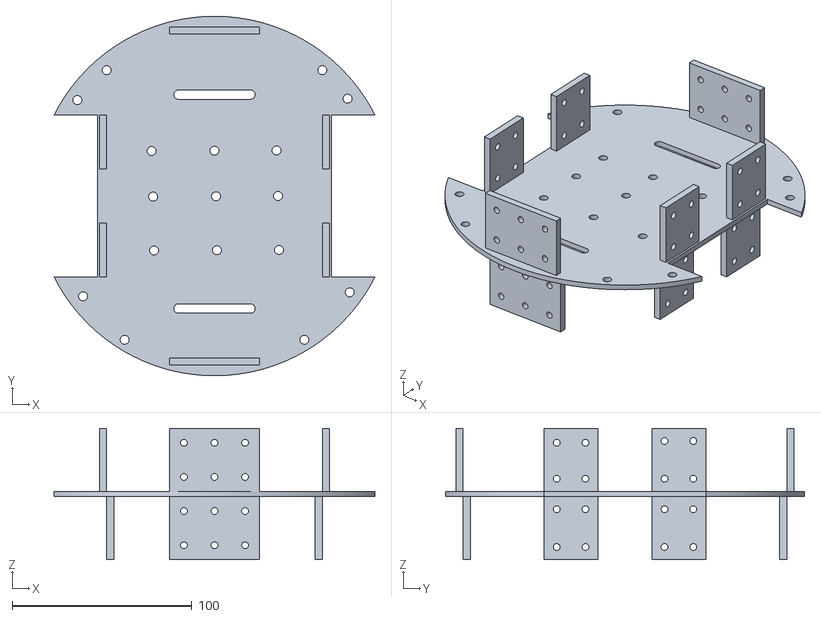
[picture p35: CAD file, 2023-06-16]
3D car design files/stl files for 3 printing/2nd - floor.stl
178.6 x 199.9 x 73.0

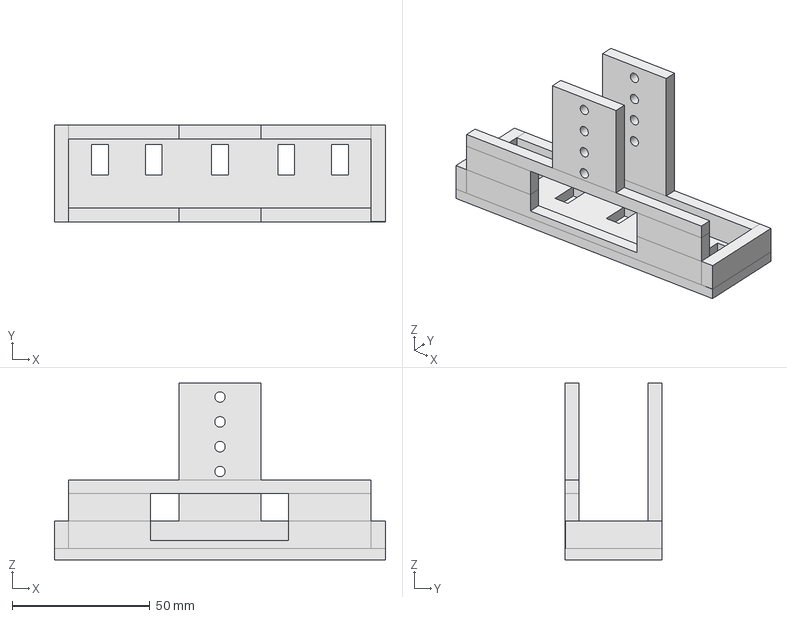
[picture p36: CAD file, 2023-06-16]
3D car design files/freeCAD-project files/sensors1.FCStd
120.0 x 35.0 x 64.0 mm

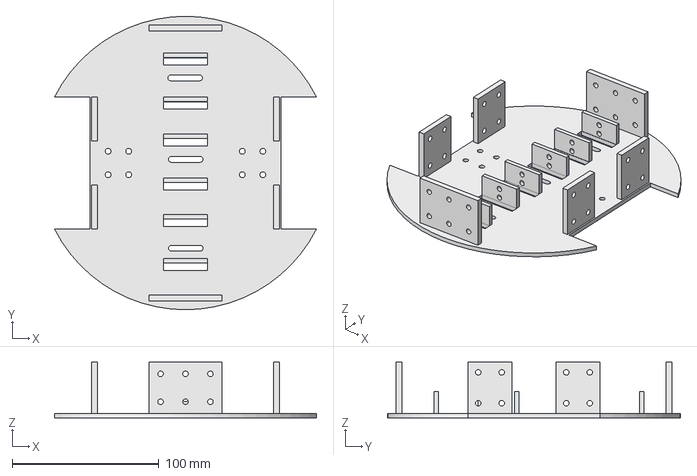
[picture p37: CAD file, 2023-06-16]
3D car design files/freeCAD-project files/first_floor.FCStd
178.6 x 200.0 x 38.0 mm

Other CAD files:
3D car design files/freeCAD-project files/second floor.FCStd
3D car design files/stl files for 3 printing/3rd - floor.stl
3D car design files/freeCAD-project files/second floor - dup.FCStd
3D car design files/stl files for 3 printing/second floor - dup.stl
3D car design files/stl files for 3 printing/sensor-Body.stl
3D car design files/stl files for 3 printing/1st - floor.stl

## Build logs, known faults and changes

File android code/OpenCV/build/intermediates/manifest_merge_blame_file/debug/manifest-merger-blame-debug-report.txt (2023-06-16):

1<?xml version="1.0" encoding="utf-8"?>
2<manifest xmlns:android="http://schemas.android.com/apk/res/android"
3    package="org.opencv" >
4
5    <uses-sdk android:minSdkVersion="21" />
5-->D:\codes\PROJECTS\third year\second term\embedded systems\Carcotech\android code\OpenCV\java\AndroidManifest.xml
6
7</manifest>

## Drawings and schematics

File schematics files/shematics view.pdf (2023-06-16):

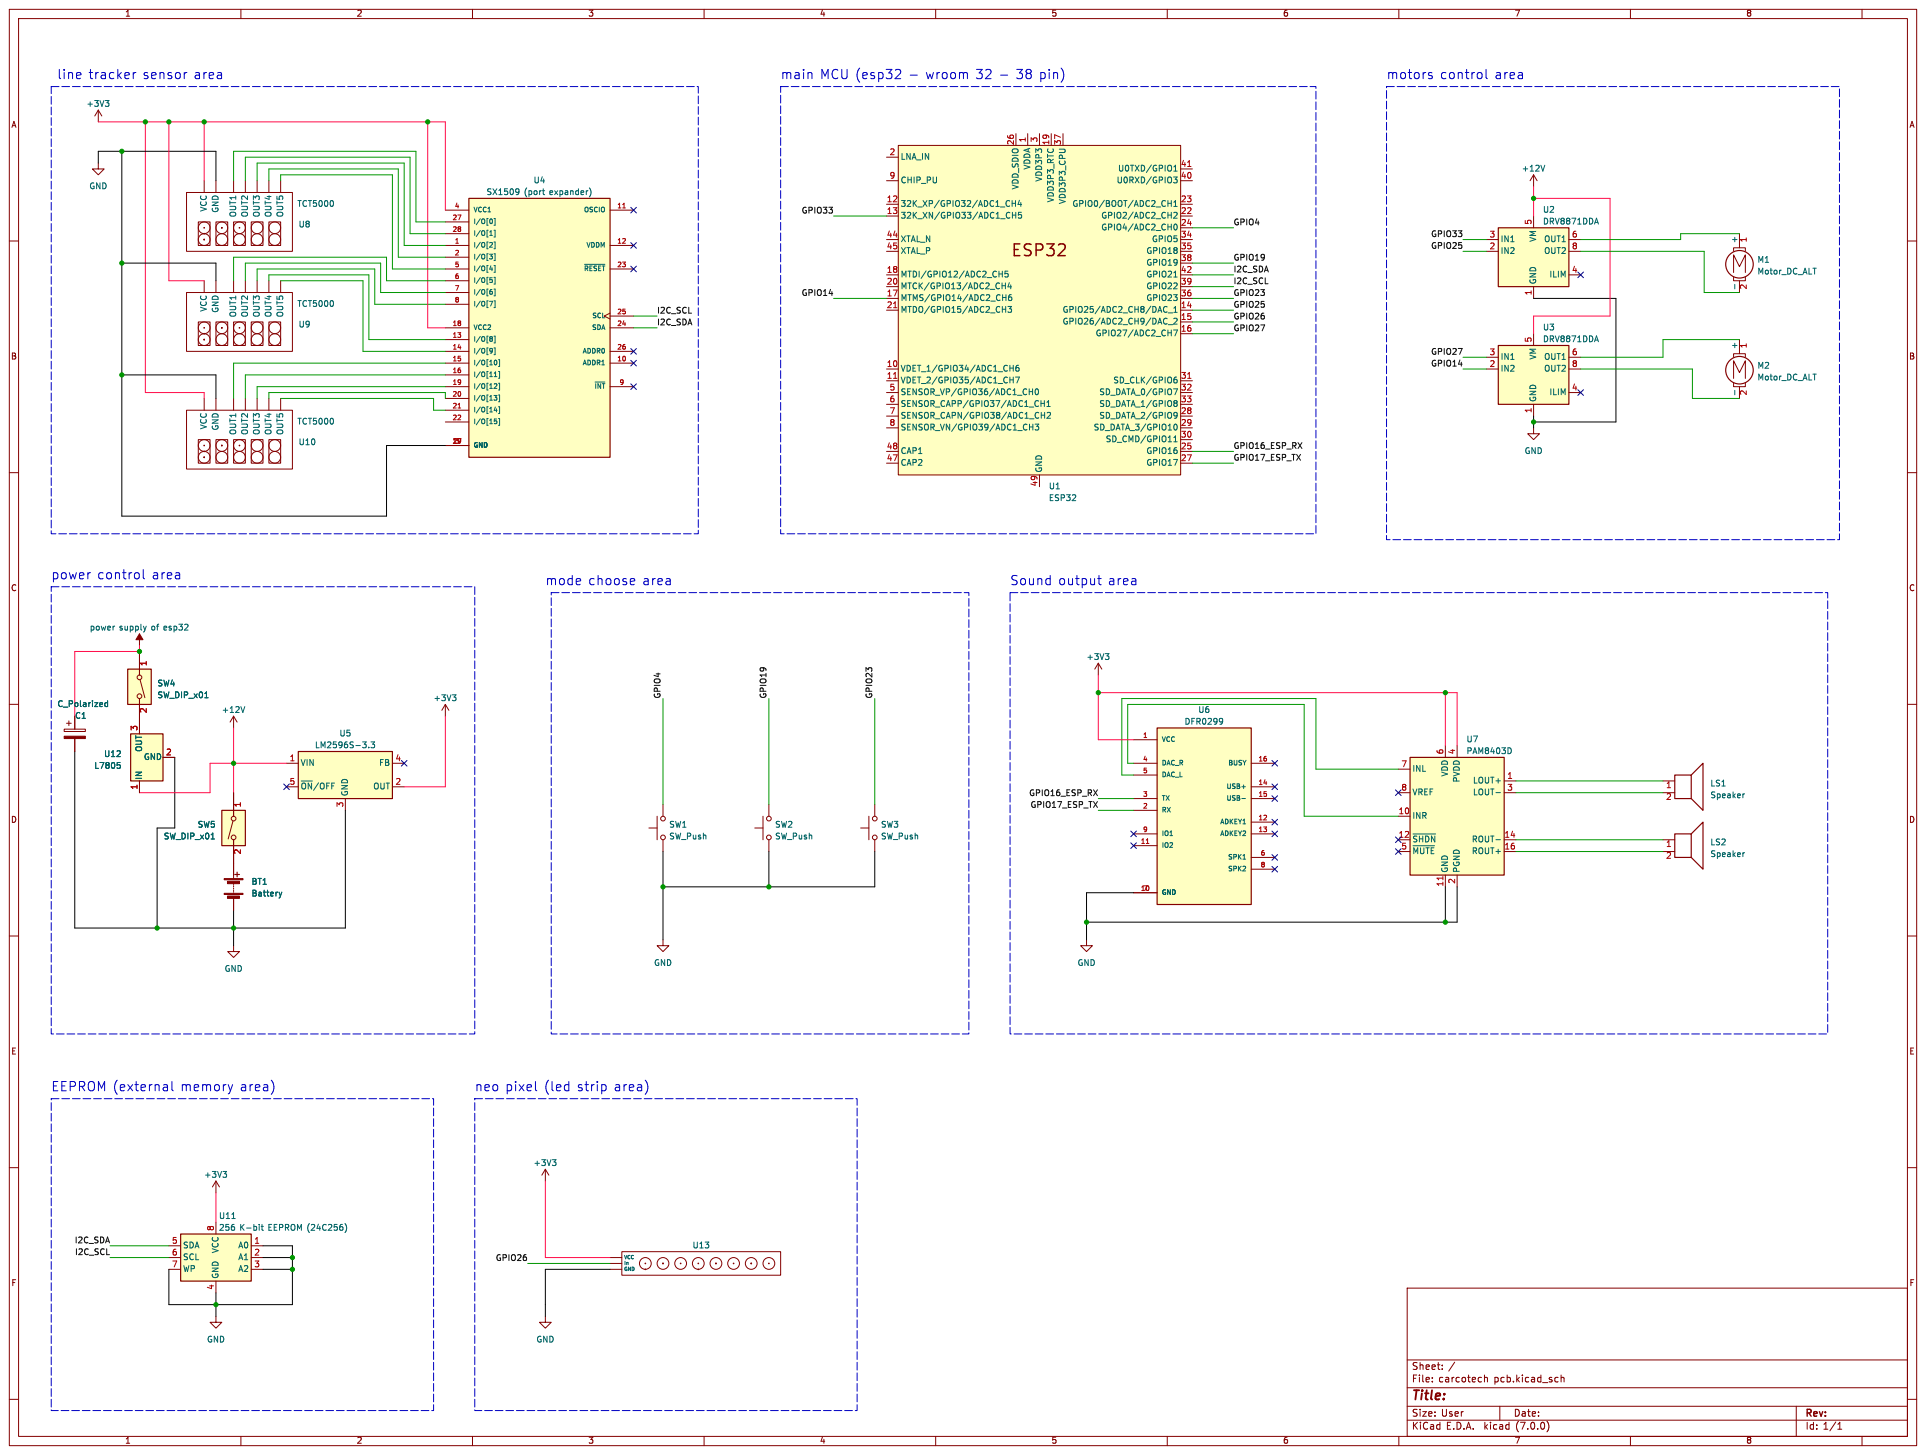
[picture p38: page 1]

line tracker sensor area
+3V3 GND

Sound output area main MCU (esp32 - wroom 32 - 38 pin)

EEPROM (external memory area) SW5 SW_DIP_x01

neo pixel (led strip area)

4 SDA 5 SCL 6 WP 7 VCC

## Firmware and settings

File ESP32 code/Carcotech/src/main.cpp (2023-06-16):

#include <Arduino.h>

#include "main.h"
#include "sensor.h"
#include "bluetooth.h"
#include "button.h"
#include "mp3.h"
#include "motor.h"
#include "Wire.h"
#include "I2C_eeprom.h"                             /*https://github.com/RobTillaart/I2C_EEPROM*/
#include "neopixel.h"

#include "utils.h"
#include "linkedList.h"

// utility objects
Bluetooth bluetooth;                                /*this is the object throught which we can control the bluetooth*/
Sensor sensor;                                      /*this is the sensor object which is used to read the sensors values*/    
Button buttons;                                     /*this is the object that will represent our interface buttons*/
MP3 mp3;                                            /*this is the player through which we can play songs*/  
Motor motor;                                        /*this is the motor driver through which we can control the motor*/
Util  util;                                         /*this is a utility object that holds some useful functions*/
LinkedList linkedList;                              /*this is a utility object that will deal with our traverse array*/
I2C_eeprom eeprom(0x50, I2C_DEVICESIZE_24LC256);    /*this is the eeprom that will store the optimized path in eeprom in order not to be lost*/
NeoPixel neopixel;                                  /*this is the neopixel led strip connected to esp32*/

// global useful variables
uint32_t pathSize = 0;                            /*this is the size of the extracted path from the eeprom*/
uint32_t pathCounter = 0;                         /*this is a counter that counts how many intersections exexuted from the path*/
uint8_t ledState = LED_STATE_RADNOM_EFFECT;       /*this is the status that represents which state of leds to use*/
uint8_t scanArr[3] = {WHITE, WHITE, WHITE};       /*this is the scan matrix used to indicate which case we are in when we stop*/   
uint8_t maxLineSpeed = LOWER_LINE_SPEED;          /*this is the speed which is set by the mobile that will tell us wether to lower to higher this value*/
uint8_t* path1 = nullptr;                         /*this is the extracted path while the car is going on its way from start to end*/
uint8_t* path2 = nullptr;                         /*this is the extracted path while the car is going on its way from end to start*/
uint32_t pathSize1 = 0;                           /*this is the size of path while the car is going on its way from start to end*/
uint32_t pathSize2 = 0;                           /*this is the size of path while the car is going on its way from end to start*/


// task handlers
TaskHandle_t xHandle_bluetoothSendData = NULL;    /*this is the task handler for the bleutooth send data task*/
TaskHandle_t xHandle_bluetoothReceiveData = NULL; /*this is the task handler for the bleutooth receive data task*/
TaskHandle_t xHandle_lineTracker = NULL;          /*this is the task handler for the line tracker task*/
TaskHandle_t xHandle_mazeTrainer = NULL;          /*this is the task handler for the maze trainer task*/
TaskHandle_t xHandle_mazeSolver = NULL;           /*this is the task handler for the maze solver task*/
TaskHandle_t xHandle_taskManager = NULL;          /*this is the task handler for the task manager*/
TaskHandle_t xHandle_ledStrip = NULL;             /*this is the task handler for the led strip*/


/*struct used by bluetooth receive data task*/
typedef struct
{
  uint8_t data[BLUETOOTH_MSG_RCV_LEN];
}bluetoothRcvMsg_t;



/**
 * @brief this function increases the speed of one of the wheels to align to the line
 * @param sensorsReading: this is a matrix holding all the readings of the matrix of sensors
*/
void align(uint8_t (*sensorsReading)[5])
{
  /*this the index of the front row*/
  uint8_t frontRowIndex = 2;

  /*main condition whether or not to preform aliging*/
  if(sensorsReading[frontRowIndex][2] == WHITE && sensorsReading[frontRowIndex][0] == WHITE && sensorsReading[frontRowIndex][4] == WHITE)
  {

    /*align left*/
    if(sensorsReading[frontRowIndex][1] == BLACK){
      motor.setDirection(MOTOR_DIR_FORWARD, MOTOR_DIR_FORWARD);
      motor.setSpeed(MAZE_LINE_SPEED, MAZE_LINE_SPEED+MAZE_ALIGN_DIFF_SPEED);
    }
    
    /*align right*/
    else if(sensorsReading[frontRowIndex][3] == BLACK){
      motor.setDirection(MOTOR_DIR_FORWARD, MOTOR_DIR_FORWARD);
      motor.setSpeed(MAZE_LINE_SPEED+MAZE_ALIGN_DIFF_SPEED, MAZE_LINE_SPEED);
    }
    
    /*return back without alignment*/
    else
      return;
      

    /*wait till the car go back in the middle again*/
    do
    {
      sensorsReading = sensor.readAverageSensor(MIN_NUM_OF_READINGS);
      if(sensorsReading[frontRowIndex][0] == BLACK || sensorsReading[frontRowIndex][4] == BLACK 
        || (sensorsReading[frontRowIndex][2] == WHITE && sensorsReading[frontRowIndex][1] == WHITE && sensorsReading[frontRowIndex][3] == WHITE))
        break;
    } while (!(sensorsReading[frontRowIndex][2] == BLACK && sensorsReading[frontRowIndex][1] == WHITE && sensorsReading[frontRowIndex][3] == WHITE));
    
    
    /*return back to the orignal speed*/
    motor.setDirection(MOTOR_DIR_FORWARD, MOTOR_DIR_FORWARD);
    motor.setSpeed(MAZE_LINE_SPEED, MAZE_LINE_SPEED);

  }

}


/**
 * @brief this function constructs the scan array as while the car moving
 * @param sensorsReading: this is a matrix holding all the readings of the matrix of sensors
 * @return bool which is a bool variable telling wehther or not to allign
*/
bool scan(uint8_t (*sensorsReading)[5])
{
  /*local variable to indicate whether or not to preform aligning or not in ( we don't preform aligning incase we met a fork)*/
  bool align = true;

  /*this the index of the front row*/
  uint8_t frontRowIndex = 2;

  /*left fork*/
  if(sensorsReading[frontRowIndex][0] == BLACK){
    scanArr[0] = BLACK;
    align = false;
  }

  /*right fork*/
  if(sensorsReading[frontRowIndex][4] == BLACK){
    scanArr[2] = BLACK;
    align = false;
  }

  return align;
}

/**
 * @brief this function only converts the scanArray to valuable information where:
 *                ->  scanArr = {BLACK , WHITE, WHITE}    incase that the there is left fork
 *                ->  scanArr = {WHITE , WHITE, BLACK}    incase that there is a right fork
 *                ->  scanArr = {BLACK , WHITE, BLACK}    incase that there is 'T' fork
 *                ->  scanArr = {WHITE , BLACK, BLACK}    incase that there is 'T' fork rotated by 90     
 *                ->  scanArr = {BLACK , BLACK, WHITE}    incase that there is 'T' fork rotated by -90
 *                ->  scanArr = {BLACK , BLACK, BLACK}    incase that there is a '+' fork
 *                ->  scanArr = {WHITE , WHITE, WHITE}    incase that is a deadend
 * @return unit8_t which detects the status of the fork, refer to @CAR_FORK_CASE
*/
uint8_t evaluateScanArray()
{ 
  if(scanArr[0] == BLACK && scanArr[1] == WHITE && scanArr[2] == WHITE)
    return LINE_FORK_LEFT;

  else if(scanArr[0] == WHITE && scanArr[1] == WHITE && scanArr[2] == BLACK)
    return LINE_FORK_RIGHT;

  else if(scanArr[0] == BLACK && scanArr[1] == WHITE && scanArr[2] == BLACK)
    return LINE_FORK_T;

  else if(scanArr[0] == BLACK && scanArr[1] == BLACK && scanArr[2] == BLACK)
    return LINE_FORK_CROSS;

  else if(scanArr[0] == WHITE && scanArr[1] == WHITE && scanArr[2] == WHITE)
    return LINE_FORK_DEADEND;
  
  else if(scanArr[0] == WHITE && scanArr[1] == BLACK && scanArr[2] == BLACK)
    return LINE_FORK_T_ANG_90;

  else if(scanArr[0] == BLACK && scanArr[1] == BLACK && scanArr[2] == WHITE)
    return LINE_FORK_T_ANG_NEG_90;

  else
    return UNDEFINED_BEHAVIOUR;
}



/**
 * @brief this function is used to make the car move forward, this usaually happens by making both of the motor wheels move in same direction
 *        till sensors[middleRow][0th Index || 4th Index] = BLACK  or sensors[frontRow][*] = WHITE then stop the motors as there is fork in the line and return case of the fork
 * @return uint8_t which represents the case through which current fork case, refer to @CAR_FORK_CASE
*/
uint8_t moveForwardTillBlackLine()
{

  /*local variables used in reading sensors values*/
  uint8_t (*sensorsReading)[5];   

  /*this is the variable that indicates what is the front row*/
  uint8_t frontRowIndex;

  /*this is a variable that indicates the status of the fork*/
  uint8_t forkStatus = UNDEFINED_BEHAVIOUR;

  /*this is a variable the will hold the stop condition*/
  bool stopCondition = false;
  
  /*the front row now is the actual fron row*/
  frontRowIndex = 2;

  /*assign the direction to the motor*/
  motor.setDirection(MOTOR_DIR_FORWARD, MOTOR_DIR_FORWARD);

  /*assign the initial speed to the motor*/
  motor.setSpeed(MAZE_LINE_SPEED, MAZE_LINE_SPEED);

  /*begin looping till the end condition*/
  do
  {
    /*read sonsor data*/
    sensorsReading = sensor.readAverageSensor(MIN_NUM_OF_READINGS);
    
    /*construct scan array*/
    bool executeAlign = scan(sensorsReading);

    /*align the motor to the line*/
    if(executeAlign)
      align(sensorsReading);

    /*there is comming fork so stop when arriving (evaluate stop condition)*/
    if(!executeAlign){
      do
        {
          sensorsReading = sensor.readAverageSensor(MIN_NUM_OF_READINGS);
          stopCondition = (sensorsReading[1][0] == BLACK) || (sensorsReading[1][4] == BLACK);

          /*just in case the forward sensors didn't get it right*/
          if(sensorsReading[1][0] == BLACK || sensorsReading[frontRowIndex][0] == BLACK)
            scanArr[0] =  BLACK;
          if(sensorsReading[1][4] == BLACK || sensorsReading[frontRowIndex][4] == BLACK)
            scanArr[2] =  BLACK;
          
        } while (!stopCondition);
  
      break;
    }
    
    /*stop whenever there is a dead end*/
    stopCondition = (sensorsReading[1][0] == WHITE && sensorsReading[1][1] == WHITE && sensorsReading[1][2] == WHITE && sensorsReading[1][3] == WHITE && sensorsReading[1][4] == WHITE 
                      && sensorsReading[frontRowIndex][2] == WHITE && sensorsReading[frontRowIndex][1] == WHITE && sensorsReading[frontRowIndex][3] == WHITE);

    
  } while (!(stopCondition));
  
  /*check for a forward black line*/
  if(sensorsReading[frontRowIndex][2] == BLACK || sensorsReading[frontRowIndex][1] == BLACK || sensorsReading[frontRowIndex][3] == BLACK)
    scanArr[1] = BLACK;


  /*get the status of the fork*/
  forkStatus = evaluateScanArray();

  /*check if we reached the end of the maze*/
  sensorsReading = sensor.readAverageSensor(MIN_NUM_OF_READINGS);
  if(sensorsReading[frontRowIndex][0] == BLACK && sensorsReading[frontRowIndex][1] == BLACK && sensorsReading[frontRowIndex][2] == BLACK && sensorsReading[frontRowIndex][3] == BLACK && sensorsReading[frontRowIndex][4] == BLACK)
    forkStatus = LINE_FORK_END;

  /*clear the scan array*/
  scanArr[0] = WHITE;
  scanArr[1] = WHITE;
  scanArr[2] = WHITE;

  /*construct the state of the fork*/
  return forkStatus;

}


/**
 * @brief this function makes the car moves from the round black circle to the straight black line, it does this simply by moving forward,
 * with aligning till the middle isn't black completly
*/
void moveFromBlackCircleToBlackLine()
{
  /*local variables used in reading sensors values*/
  uint8_t (*sensorsReading)[5]; 

  /*set speed and direction of the car*/
  motor.setDirection(MOTOR_DIR_FORWARD, MOTOR_DIR_FORWARD);
  motor.setSpeed(MAZE_LINE_SPEED, MAZE_LINE_SPEED);

  /*move forward till exit the black circle*/
  do
  {
    sensorsReading = sensor.readAverageSensor(MIN_NUM_OF_READINGS);
  }while(sensorsReading[1][0] == BLACK && sensorsReading[1][1] == BLACK && sensorsReading[1][2] == BLACK && sensorsReading[1][3] == BLACK && sensorsReading[1][4] == BLACK);

}

/**
 * @brief this function is used to make the car turn left by 90 degree, this usaually happens by making one of the motor wheels move in direction
 *        while the other wheel moves in the reverse direction then rotate till read the (sensors[frontRow][0th index] = WHITE)  then 
 *        rotate again in the same direction till (sensors[frontRow][middle index] = BLACK and sensors[frontRow][middle index-1] = WHITE and sensors[frontRow][middle index+1] = BLACK) then continue moving forward
*/
void turnLeftTillBlackLine()
{
  /*this is a variable that indicates which sensor array to read from*/
  uint8_t frontRowIndex = 2;

  /*local variables used in reading sensors values*/
  uint8_t (*sensorsReading)[5]; 

  /*set the direction of the motors*/
  motor.setDirection(MOTOR_DIR_BACKWARD, MOTOR_DIR_FORWARD);
  motor.setSpeed(MAZE_LINE_SPEED_OPPOSITE_DIR, MAZE_LINE_SPEED);
  
  /*rotate till the car front sensor become in the white space*/
  do
  {
    sensorsReading = sensor.readAverageSensor(MIN_NUM_OF_READINGS);
  } while (sensorsReading[frontRowIndex][2] == BLACK || sensorsReading[frontRowIndex][0] == WHITE);

  /*continue rotating till the sensor return back to the black line again*/
  do
  {
    sensorsReading = sensor.readAverageSensor(MIN_NUM_OF_READINGS);
  } while (!(sensorsReading[frontRowIndex][2] == BLACK && sensorsReading[frontRowIndex][1] == WHITE && sensorsReading[frontRowIndex][3] == WHITE));

}

/**
 * @brief this function is used to make the car turn right by 90 degree, this usaually happens by making one of the motor wheels move in direction
 *        while the other wheel moves in the reverse direction then rotate till read the (sensors[frontRow][0th index] = WHITE)  then 
 *        rotate again in the same direction till (sensors[frontRow][middle index] = BLACK and sensors[frontRow][middle index-1] = WHITE and sensors[frontRow][middle index+1] = BLACK) then continue moving forward
*/
void turnRightTillBlackLine()
{
  /*this is a variable that indicates which sensor array to read from*/
  uint8_t frontRowIndex = 2;

  /*local variables used in reading sensors values*/
  uint8_t (*sensorsReading)[5]; 

  /*set the direction of the motors*/
  motor.setDirection(MOTOR_DIR_FORWARD, MOTOR_DIR_BACKWARD);
  motor.setSpeed(MAZE_LINE_SPEED, MAZE_LINE_SPEED_OPPOSITE_DIR);
  
  /*rotate till the car front sensor become in the white space*/
  do
  {
    sensorsReading = sensor.readAverageSensor(MIN_NUM_OF_READINGS);
  } while (sensorsReading[frontRowIndex][2] == BLACK || sensorsReading[frontRowIndex][4] == WHITE);

  /*continue rotating till the sensor return back to the black line again*/
  do
  {
    sensorsReading = sensor.readAverageSensor(MIN_NUM_OF_READINGS);
  } while (!(sensorsReading[frontRowIndex][2] == BLACK && sensorsReading[frontRowIndex][1] == WHITE && sensorsReading[frontRowIndex][3] == WHITE));

}


/**
 * @brief this function is used to make the car turn right by 180 degree, this usaually happens by making one of the motor wheels move in direction
 *        while the other wheel moves in the reverse direction then rotate till read the (sensors[frontRow][2th index] = BLACK) wthen continue moving forward
*/
void UTurnTillBlackLine()
{
  /*this is a variable that indicates which sensor array to read from*/
  uint8_t frontRowIndex = 2;

  /*local variables used in reading sensors values*/
  uint8_t (*sensorsReading)[5]; 

  /*set the direction of the motors*/
  motor.setDirection(MOTOR_DIR_BACKWARD ,MOTOR_DIR_FORWARD);
  motor.setSpeed(MAZE_LINE_SPEED_OPPOSITE_DIR, MAZE_LINE_SPEED);
  
  /*rotate till the car front sensor become on the line again*/
  do
  {
    sensorsReading = sensor.readAverageSensor(MIN_NUM_OF_READINGS);
  } while (sensorsReading[frontRowIndex][2] == WHITE);

}

/**
 * @brief this function is used to make a u-turn when reaching the end so that it can visit an extra path, this usaually happens by making one of the motor wheels move in direction
 *        while the other wheel moves in the reverse direction then rotate till read the (sensors[frontRow][2th index] = WHITE) hen rotate till read the (sensors[frontRow][2th index] = BLACK) 
 *        then continue moving forward
*/
void UTurnAtEndCircle()
{
  /*this is a variable that indicates which sensor array to read from*/
  uint8_t frontRowIndex = 2;

  /*local variables used in reading sensors values*/
  uint8_t (*sensorsReading)[5]; 

  /*return back till the begin of the line*/
  motor.setDirection(MOTOR_DIR_BACKWARD , MOTOR_DIR_BACKWARD);
  motor.setSpeed(MAZE_LINE_SPEED_OPPOSITE_DIR, MAZE_LINE_SPEED_OPPOSITE_DIR);
  do
  {
    sensorsReading = sensor.readAverageSensor(MIN_NUM_OF_READINGS);
  } while ((sensorsReading[1][0] == BLACK || sensorsReading[1][1] == BLACK) && (sensorsReading[1][3] == BLACK || sensorsReading[1][4] == BLACK));

  /*wait for motor to stop*/
  motor.stop();
  vTaskDelay(pdMS_TO_TICKS(STOP_DELAY));

  /*set the direction of the motors*/
  motor.setDirection(MOTOR_DIR_BACKWARD ,MOTOR_DIR_FORWARD);
  motor.setSpeed(MAZE_LINE_SPEED_OPPOSITE_DIR, MAZE_LINE_SPEED);

  /*rotate till the car front sensor become on the line again*/
  do
  {
    sensorsReading = sensor.readAverageSensor(MIN_NUM_OF_READINGS);
  } while (sensorsReading[frontRowIndex][2] == BLACK);

  /*rotate till the car front sensor become on the line again*/
  do
  {
    sensorsReading = sensor.readAverageSensor(MIN_NUM_OF_READINGS);
  } while (sensorsReading[frontRowIndex][2] == WHITE);

}


/**
 * @brief this is the task used for receiving data by esp32 from a mobile using bluetooth to change the max speed value on the line
*/
void receiveData(void* pvParameters)
{
  /*for sending and receiving structs*/
  bluetoothRcvMsg_t receivedMsg;

  /*suspend the bluetooth task*/
  /*docs: https://www.freertos.org/a00130.html */
  vTaskSuspend(NULL);

  while (true)
  {

    /*receiving message form the receiver from the receiver and put it in a queue to be send back*/
    strcpy((char*)receivedMsg.data, bluetooth.getData(BLUETOOTH_MSG_RCV_LEN, 0).c_str());

    /*for some reason we received an empty message*/
    if(receivedMsg.data[0] != '\0' && receivedMsg.data[0] != '\n') 
    {
      
      /*check for the sent character*/
      if(receivedMsg.data[0] == 'h' || receivedMsg.data[0] == 'H')
      {
        /*the mobile app let us use the maximum speed*/
        maxLineSpeed = UPPER_LINE_SPEED;
      }
      else if(receivedMsg.data[0] == 'l' || receivedMsg.data[0] == 'L')
      {
        /*the mobile app prohibited us from using the maximum speed*/
        maxLineSpeed = LOWER_LINE_SPEED;
      }
      else
      {
        // invalid char so do nothing
      }

    }

    /*to preform context switching*/
    taskYIELD();
  }

  /*to prevent a task from returning as if the task returned, it will cause an exception*/
  /*docs: https://www.freertos.org/a00126.html */
  vTaskDelete(NULL);

}

/**
 * @brief this is the task used for line tracker
*/
void lineTracker(void *pvParamters)
{ 

  while (true)
  {

    /*this is a flag to indicate whether user wanted to end the line tracker or not*/
    bool endLineTracker = false; 

    /*wait for a notification from the task manager*/
    /*docs: https://www.freertos.org/ulTaskNotifyTake.html */
    ulTaskNotifyTake(pdTRUE, portMAX_DELAY);

    /*begin the song*/
    mp3.changeSong(YA_SAYAED, false);

    /*local variables used in reading sensors values*/
    uint8_t (*sensorsReading)[5];   

    /*assign the direction to the motor*/
    motor.setDirection(MOTOR_DIR_FORWARD, MOTOR_DIR_FORWARD);

    do
    {
        
      /*assign the initial speed to the motor*/
      motor.setSpeed(maxLineSpeed, maxLineSpeed);

      /*get the readings of the sensors*/
      sensorsReading = sensor.readAverageSensor(MIN_NUM_OF_READINGS);

      /*check for the case of the sensors whether to align or not*/
      if(sensorsReading[2][0] == WHITE && sensorsReading[2][1] == WHITE && (sensorsReading[2][3] == BLACK || sensorsReading[2][4] == BLACK))
      { 
        /*align right*/
        motor.setDirection(MOTOR_DIR_FORWARD, MOTOR_DIR_FORWARD);
        motor.setSpeed(CURVE_SPEED, MAX_SPEED);
        do
        {
          sensorsReading = sensor.readAverageSensor(MIN_NUM_OF_READINGS);
        } while (sensorsReading[2][2] == WHITE);

        /*return to original forward speed*/
        motor.setDirection(MOTOR_DIR_FORWARD, MOTOR_DIR_FORWARD);
        motor.setSpeed(maxLineSpeed, maxLineSpeed);

      }
      else if ((sensorsReading[2][0] == BLACK || sensorsReading[2][1] == BLACK) && sensorsReading[2][3] == WHITE && sensorsReading[2][4] == WHITE)
      {
        /*align left*/
        motor.setDirection(MOTOR_DIR_FORWARD, MOTOR_DIR_FORWARD);
        motor.setSpeed(MAX_SPEED, CURVE_SPEED);
        do
        {
          sensorsReading = sensor.readAverageSensor(MIN_NUM_OF_READINGS);
        } while (sensorsReading[2][2] == WHITE);

        /*return to original forward speed*/
        motor.setDirection(MOTOR_DIR_FORWARD, MOTOR_DIR_FORWARD);
        motor.setSpeed(maxLineSpeed, maxLineSpeed);
      }
      else
      {
        // do nothing
      }

      /*check if user wanted to end the line tracker task*/
      if(buttons.isBeginLineTrackingPressed())
      {
        /*stop the motor*/
        motor.stop();

        /*give control back to user*/
        endLineTracker = true;    

        /*stop play the music*/
        mp3.stopMusic();  

        /*delay for button debouncing*/
        vTaskDelay(pdMS_TO_TICKS(250)); 
      }

    }while(endLineTracker == false);

    /*wake up the task manager to tell it that I finished*/
    /*docs: https://www.freertos.org/xTaskNotifyGive.html */
    xTaskNotifyGive(xHandle_taskManager);   

  }
  
  /*safety: preventy the task from returning*/
  /*docs: https://www.freertos.org/a00126.html */
  vTaskDelete(NULL);

}
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
void loop() {
  /*this is the idle task, it will not be executed as its priority is tskIDLE_PRIORITY, the only case when this task will be executed is
    when all other tasks are suspended or at maximum 1 task is executing as this MCU is dual core*/
}

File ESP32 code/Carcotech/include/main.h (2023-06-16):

#ifndef CONSTANTS_H_
#define CONSTANTS_H_

#include "soc/rtc_wdt.h"

// specific led modes
#define LED_STATE_BATTERY_EFFECT    0
#define LED_STATE_RADNOM_EFFECT     1
#define LED_STATE_BLUETOOTH         2


// specific speeds used by the line tracker
#define MAX_SPEED           110     // this is the speed of the lower speed wheel when taking curves 
#define CURVE_SPEED         240     // this is the speed of the higher speed wheel when taking curves
#define UPPER_LINE_SPEED    250     // this is the speed that we will use in case of straight line and the mobile app allowed us to use max speed
#define LOWER_LINE_SPEED    210     // this is the speed that we will use in case of straight line and the mobile app didn't allow us to use max speed


// specific speeds used by the maze
#define MAZE_LINE_SPEED                 110 //100
#define MAZE_ALIGN_DIFF_SPEED           100
#define MAZE_LINE_SPEED_OPPOSITE_DIR    150 //150
#define STOP_DELAY                      100


// this is the fork status @CAR_FORK_CASE
#define LINE_FORK_CROSS         0           // which looks like the plus sign + so possible directions are right, left and forward
#define LINE_FORK_T             1           // which looks like letter T so possible directions are right and left
#define LINE_FORK_T_ANG_90      2           // which looks like letter T but rotated with angle 90 so possible directions are right and forward
#define LINE_FORK_T_ANG_NEG_90  3           // which looks like letter T but rotated with angle -90 so possible directions are left and forward
#define LINE_FORK_LEFT          4           // which means a left only branch so possible directions are only left
#define LINE_FORK_RIGHT         5           // which means a right only branch  so possible directions are only right
#define LINE_FORK_DEADEND       6           // this is a deadlock line so no possible directions
#define LINE_FORK_END           7           // this is the end of the maze so stop 


// related to the bluetooth task
#define BLUETOOTH_STACK_SEND_DATA       1024      // used by freeRTOS to create task for sending data
#define BLUETOOTH_MSG_SEND_LEN          5       // used by queues for sending data to the task
#define BLUETOOTH_SEND_DATA_QUEUE_LEN   10      // used by queues to create the length of the queue

#define BLUETOOTH_STACK_RCV_DATA       1024      // used by freeRTOS to create task for sending data
#define BLUETOOTH_MSG_RCV_LEN          1       // used by queues for sending data to the task
#define BLUETOOTH_RCV_DATA_QUEUE_LEN   10      // used by queues to create the length of the queue


// related to line tracker task 
#define LINE_TRACKER_STACK_DATA        2048     // used by freeRTOS to crate task for tracking line


// related to maze trainer task     
#define MAZE_TRAINER_STACK_DATA        2048     // used by freeRTOS to crate task for training on the maze to solve it

// related to maze solver task         
#define MAZE_SOLVER_STACK_DATA         2048     // used by freeRTOS to crate task for solving the maze

// related to task manager task
#define TASK_MANAGER_STACK_DATA        1024     // used by freeRTOS to crate task for creating a task that manages other tasks

// related to led strip tasl   
#define LED_STRIP_STACK_DATA           1024     // used by freeRTOS to crate task for manipulating leds


// related to EEPROM
#define STORE_ADDR      0           // this is the address that we will begin storing the values in it


// related to the sensor
#define MIN_NUM_OF_READINGS     2  // used to read stable value where the sensor is determined to be stable when reading 10 times has same readings


// undefined behaviour define
#define UNDEFINED_BEHAVIOUR         255

// time period of alignments
#define TIME_PERIOD_ALIGNM_MS       10


#endif

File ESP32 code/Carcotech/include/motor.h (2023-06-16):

#ifndef MOTOR_H_
#define MOTOR_H_

#include <Arduino.h>

// note that IN1 will represent direction while IN2 will represent the speed

// motor speed channels
#define MOTOR_L_SPEED_CHANNEL   0
#define MOTOR_R_SPEED_CHANNEL   1


// related to the motor pins
#define MOTOR_L_IN1_PIN     33      // direction pin
#define MOTOR_L_IN2_PIN     32      // speed pin

#define MOTOR_R_IN1_PIN     27      // direction pin
#define MOTOR_R_IN2_PIN     13      // speed pin


// @POSSIBLE_SPEED_VALS_PWM
#define MOTOR_SPEED_BREAK    0
#define MOTOR_SPEED_1       25
#define MOTOR_SPEED_2       50
#define MOTOR_SPEED_3       75
#define MOTOR_SPEED_4       100
#define MOTOR_SPEED_5       125
#define MOTOR_SPEED_6       150
#define MOTOR_SPEED_7       175
#define MOTOR_SPEED_8       200
#define MOTOR_SPEED_9       225
#define MOTOR_SPEED_MAX     255


// @POSSIBLE_DIRECTION
#define MOTOR_DIR_FORWARD   1
#define MOTOR_DIR_BACKWARD  0

// @WHICH_MOTOR
#define MOTOR_LEFT          0
#define MOTOR_RIGHT         1


class Motor
{
private:

    /*this is the current speed of the left wheel*/
    uint8_t leftWheelSpeed = 0;

    /*this is the current speed of the right wheel*/
    uint8_t rightWheelSpeed = 0;
    
    /*this is the current direction of the left wheel*/
    uint8_t leftWheelDirection = MOTOR_DIR_FORWARD;

    /*this is the current direction of the right wheel*/
    uint8_t rightWheelDirection = MOTOR_DIR_FORWARD;
    
public:

    /**
     * @brief this is the initialization function , it has to be called before using any other functions
    */
   void init();

   /**
    * @brief this function sets the speed of motor
    * @param LSpeed : this is the speed of the left wheel, refer to @POSSIBLE_SPEED_VALS_PWM to know the paramters of this function 
    * @param RSpeed : this is the speed of the right wheel,  refer to @POSSIBLE_SPEED_VALS_PWM to know the paramters of this function
   */
   void setSpeed(uint8_t LSpeed, uint8_t RSpeed);

    /**
     * @brief this function controls the direction of the motor
     * @param LDirection: this is the direction of the left wheel, refer to @POSSIBLE_DIRECTION to know possible parameters
     * @param RDirection: this is the direction of the right wheel, refer to @POSSIBLE_DIRECTION to know possible parameters 
    */
   void setDirection(uint8_t LDirection, uint8_t RDirection);


    /**
     * @brief this function is used to stop the motor immediatly
    */
    void stop();

    /**
     * @brief this function is used to stop left wheel of the motor immediatly
    */
    void stopLeftWheel();

    /**
     * @brief this function is used to stop right wheel of  the motor immediatly
    */
    void stopRightWheel();

    /**
     * @brief this function is used to increase the speed of the motor wheels
     * @param leftWheelIncreaseAmount: a value between 0 to 255 that tells the incrase amount of the speed of the left wheel
     * @param righWheelIncreaseAmount: a value between 0 to 255 that tells the incrase amount of the speed of the right wheel    
    */
    void increaseMotorSpeed(uint8_t leftWheelIncreaseAmount, uint8_t rightWheelIncreaseAmount);

    /**
     * @brief this function is used to decrease the speed of the motor wheels
     * @param leftWheelDecreaseAmount: a value between 0 to 255 that tells the incrase amount of the speed of the left wheel
     * @param righWheelDecreaseAmount: a value between 0 to 255 that tells the incrase amount of the speed of the right wheel    
    */
    void decreaseMotorSpeed(uint8_t leftWheelDecreaseAmount, uint8_t rightWheelDecreaseAmount);
    
};  


#endif

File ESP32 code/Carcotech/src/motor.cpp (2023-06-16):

#include "motor.h"


void Motor::init()
{

    /*make motor direction pins as output*/
    pinMode(MOTOR_R_IN1_PIN, OUTPUT);
    pinMode(MOTOR_L_IN1_PIN, OUTPUT);

    /*put initial values on the pins*/
    digitalWrite(MOTOR_R_IN1_PIN, LOW);
    digitalWrite(MOTOR_L_IN1_PIN, LOW);
    
    /*initalize speed channels*/
    ledcSetup(MOTOR_L_SPEED_CHANNEL, 4000, 8); 
    ledcSetup(MOTOR_R_SPEED_CHANNEL, 4000, 8);

    /*assign speed control PWM channels to speed control pins*/
    ledcAttachPin(MOTOR_L_IN2_PIN, MOTOR_L_SPEED_CHANNEL);
    ledcAttachPin(MOTOR_R_IN2_PIN, MOTOR_R_SPEED_CHANNEL);

    /*intialize the pins*/
    ledcWrite(MOTOR_L_SPEED_CHANNEL, 0);
    ledcWrite(MOTOR_R_SPEED_CHANNEL, 0);

}

void Motor::setSpeed(uint8_t LSpeed, uint8_t RSpeed)
{   
    
    /*store the values of the speed*/
    leftWheelSpeed = LSpeed;
    rightWheelSpeed = RSpeed;

    /*check for the direction of left wheel to calculate the speed*/
    if(leftWheelDirection == MOTOR_DIR_FORWARD)
    {
        LSpeed = 255 - LSpeed;
    }   
    
    /*check for the direction of right wheel to calculate the speed*/
    if(rightWheelDirection == MOTOR_DIR_FORWARD)
    {
        RSpeed = 255 - RSpeed;
    }

    /*stop the left wheel*/
    if(LSpeed == MOTOR_SPEED_BREAK)
    {
      /*stop the wheel*/
      stopLeftWheel();
    }
    else
    {
      /*assign the speed to the left wheel*/
      ledcWrite(MOTOR_L_SPEED_CHANNEL, LSpeed);
    }

    /*stop the right wheel*/
    if(RSpeed == MOTOR_SPEED_BREAK)
    {
      /*stop the wheel*/
      stopRightWheel();
    }
    else
    {
      /*assign the speed to the right wheel*/
      ledcWrite(MOTOR_R_SPEED_CHANNEL, RSpeed);
    }


}

void Motor::setDirection(uint8_t LDirection, uint8_t RDirection)
{

    /*assign the direction values to variables*/
    leftWheelDirection = LDirection;
    rightWheelDirection = RDirection;

    /*check for direction of left wheel*/
    if(LDirection == MOTOR_DIR_FORWARD)
    {
        /*make left wheel move forward*/
        digitalWrite(MOTOR_L_IN1_PIN, HIGH);
    }
    else if(LDirection == MOTOR_DIR_BACKWARD)
    {
        /*make left wheel move backward*/
        digitalWrite(MOTOR_L_IN1_PIN, LOW);
    }
    else
    {
        // do nothin
    }


    /*check for the direction of the right wheel*/
    if(RDirection == MOTOR_DIR_FORWARD)
    {
        /*make right wheel move forward*/
        digitalWrite(MOTOR_R_IN1_PIN, HIGH);
    }
    else if(RDirection == MOTOR_DIR_BACKWARD)
    {
        /*make right wheel move backward*/
        digitalWrite(MOTOR_R_IN1_PIN, LOW);
    }
    else
    {
        // do nothing
    }

}
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

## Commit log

2023-03-02 implementing first stage of bluetooth Module
2023-04-10 completed sensor-Module drive for only function (readSensor) with 2 different implementations along with the init function
2023-04-11 completed basic functions of buttons
2023-04-13 completed motor driver but without feedback as that feedback is considered to be a bad idea
2023-06-16 arranged the files structures
    [1st - floor.stl, 2nd - floor.stl, 3rd - floor.stl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]
